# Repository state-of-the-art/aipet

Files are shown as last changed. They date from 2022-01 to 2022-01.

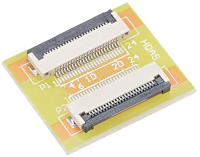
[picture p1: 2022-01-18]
doc/img/flex_to_flex.png

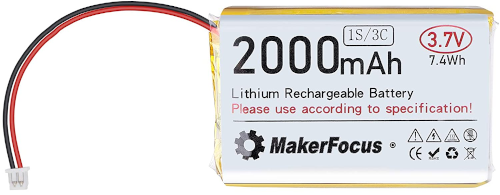
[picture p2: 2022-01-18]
doc/img/battery.png

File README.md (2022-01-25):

# AiPet

AiPet project aimed to create the AI-enchanced soft robot pet. In general it's an inflated beach
ball which contains a core with electronics and motors inside, controls pressure and position of
the core by teflon strings to move around.

It can hear by mic array, see the world via 2 cameras and use internal speakers to make noise. The
charging is wireless so it can charge itself if can find the properly placed wireless charger.

## Electric schema

Check this document to figure out: [Electric schema](doc/electric_schema.svg)

## Components

* [Sipeed Maix M1W Dock Kit K210 AI+lOT WiFi Development Board RISC-V Dual Core 64bit](https://www.amazon.com/dp/B08HJ8W1WB/)
* [Sipeed Maix Binocular Camera](https://www.amazon.com/dp/B08HH9BYTF/)
* [Sipeed Maix R6+1 Microphone Array](https://www.amazon.com/dp/B08HH799XZ/)
* [Flexible Flat Cable, 24 Pins 0.5mm Pitch 150mm FPC FFC](https://www.amazon.com/dp/B07S191XHZ/)
* [0.5mm Pitch 24 Pins to 24 Pin Extension Connector Aapter FFC FPC](https://www.amazon.com/dp/B07SWR5VP9/)
* [3.7V 2000mAh Lithium Rechargable Battery 1S 3C](https://www.amazon.com/dp/B08T6QS58J/)
* [DC 5V 9V 12V UPS Module Voltage Boost Battery Charge with Protection for Lithium Li-ion 18650 Battery](https://www.amazon.com/dp/B08LZCPVFM/)
* [6x 3V Micro Planetary Reducer Motor (9161C)](https://www.amazon.com/dp/B07N7PY71F)
* [6x custom motor driver](custom/m10_mini_dc_control/)
* [DRV8833 Motor Drive Module 1.5A Dual H Bridge](https://www.amazon.com/dp/B08RMWTDLM/)
* [2x OV2640 Camera Module T-Camera Plus Camera Module ESP32-DOWDQ6 8MB SPRAM with 1/4" OLED Fisheye Lens](https://www.amazon.com/dp/B08FC2FL79/)
* [GY-87 10DOF Module MPU6050 HMC5883L BMP180 Gyroscope Acceleration Compass](https://www.amazon.com/dp/B098JN14XV/)
* [2x Magnetic Speaker 1W 8 Ohm 20x14x3mm](https://www.amazon.com/dp/B0826YMCQ7/)
* [High Power 24V 200mm One-to-Many Long Distance Wireless Charging Pad](https://www.amazon.com/dp/B07QNF6J6Z/)

* [6x MR63ZZ 3x6x2.5mm Rolling Bearing](https://www.amazon.com/dp/B0816CL22H/)
* [16inch Clear Beach Ball](https://www.amazon.com/dp/B0943CCZLQ/)
* [6x Clear Suction Cups](https://www.amazon.com/dp/B07H5QCXR6/)
* Silicone air hose
* FDM 3D Printer

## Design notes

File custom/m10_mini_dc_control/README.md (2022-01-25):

# m10 mini dc control

This control board designed to precisely control the 9161C geared M10 mini motor with extended
shaft.

# Usage

In general you just need to connect the board to your I2C bus and power it with 5V of power (in
theory voltage regulator allows 2.5-5.5V so the motor can work on lower voltages with slower speed).

You will need to modify the `I2C_SLAVE_ADDRESS` in firmware, compile it (or use the predefined one)
and flash to the MK. After that you will be able to use as many motors as you want.

## Firmware

TODO

# Components

* 3V Micro Planetary Reducer Motor (9161C) - target motor with plastic reduction gearbox
* ATTiny 13A MMFR (DFN-10 3x3mm) - microcontroller to interface I2C and control the driver
* DRV8837C DSGR (WSON) - H-bridge driver for the motor
* MIC5365-3.3YMT-TZ (Thin MLF (MT)) - 5V to 3.3V voltage regulator to power the MK and driver logic
* QRE1113GR (100CY) - reflective object sensor to detect the motor rotation
* Various 0201 and 0402 resistors, caps and a LED

* (optional) Electrolitic capacitor to store the rest power from the motor (check driver DS)

## [3V Micro Planetary Reducer Motor (9161C)](https://www.amazon.com/dp/B07N7PY71F)

Price: $1.8 ($9 for 5pc)

### Motor specifications:

* Reduction ratio: 1:171
* Rated torque: 9.8 mN.m
* Maximum torque: 37.2 mN.m

* Rated voltage: 2.5V DC
* No-load current: 40mA
* No-load speed: 92 RPM

* Dimensions: 8x10x12mm (M10 motor)
* Planetary gearbox outer diameter: 9.9mm
* Weight: 4 grams
* Geared motor height: 19.5mm (motor + gear box)
* Output shaft: Gear with an outer diameter of 5.35mm (11 teeth)

### The following measures the motor speed under other voltages:

* Voltage: 3V
  * Current: 42mA
  * Speed: 110 RPM
* Voltage: 3.7V
  * Current: 48mA
  * Speed: 135 RPM
* Voltage: 4.2V
  * Current: 52mA
  * Speed: 154 RPM
* Voltage: 5V
  * Current: 58mA
  * Speed: 180 RPM

# How to order

Just go to your favorite PCB manufacturer and order as many boards as you want.

* [PCBWay](doc/pcbway_order.png)

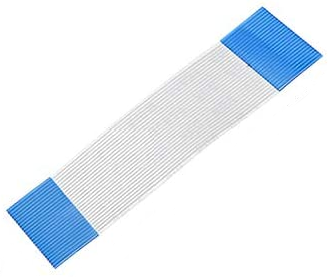
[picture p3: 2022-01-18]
doc/img/flex_camera.png

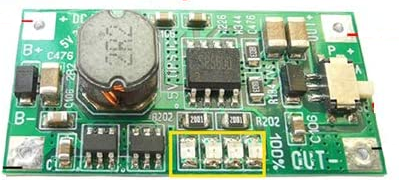
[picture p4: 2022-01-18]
doc/img/charger.png

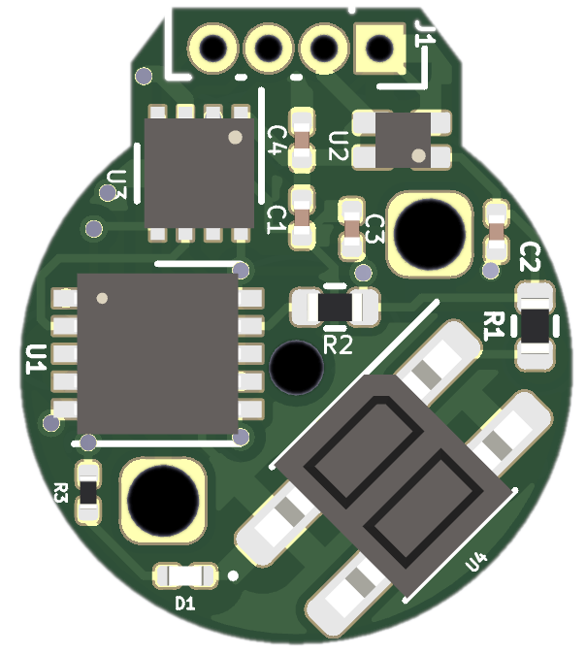
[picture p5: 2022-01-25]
doc/img/custom_motor_control.png

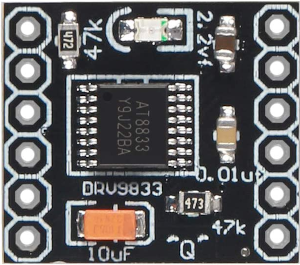
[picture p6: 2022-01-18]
doc/img/motor_driver.png

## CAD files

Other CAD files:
models/aipet.blend

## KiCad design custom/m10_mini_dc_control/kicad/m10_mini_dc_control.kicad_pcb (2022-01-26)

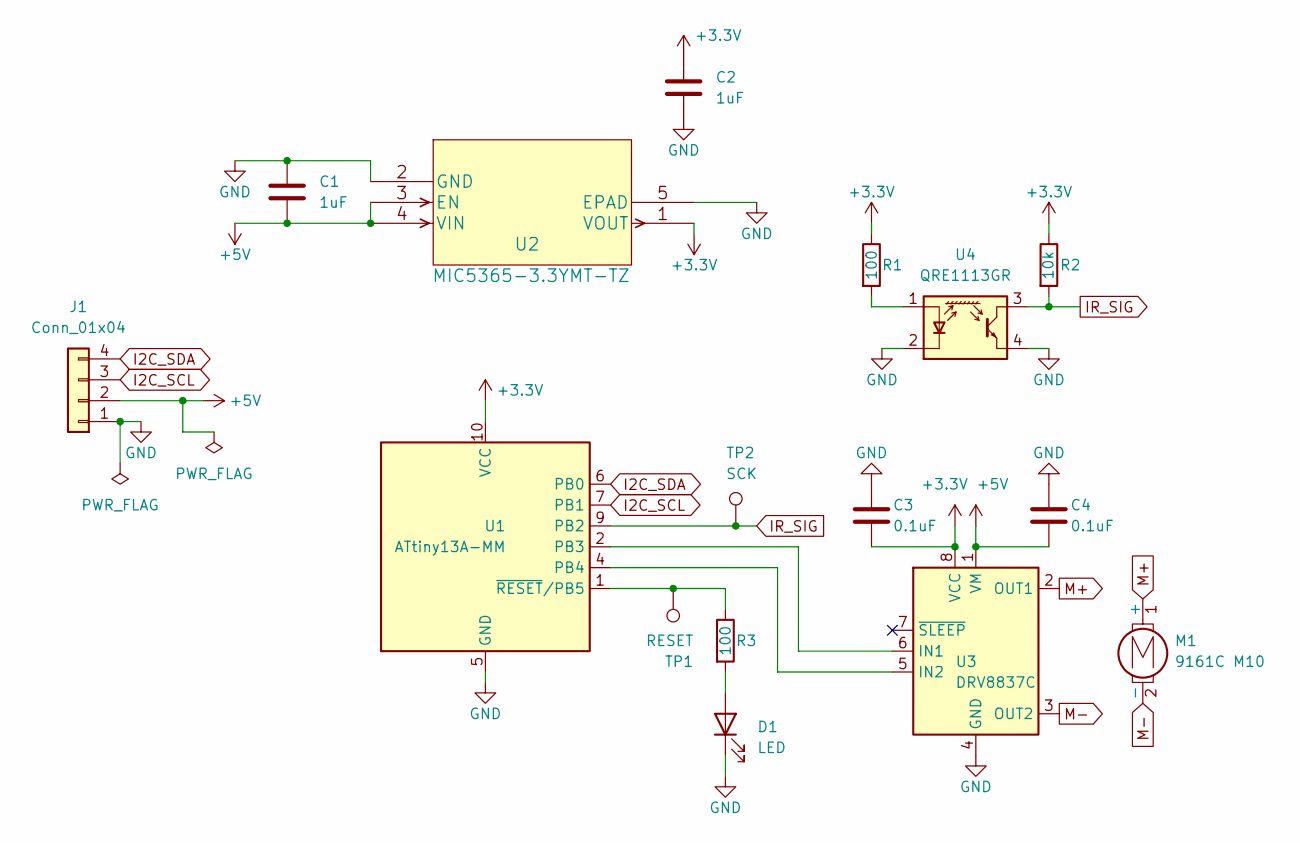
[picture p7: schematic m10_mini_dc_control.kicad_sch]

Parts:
C1, C2: 1uF; C_0201_0603Metric
C3, C4: 0.1uF; C_0201_0603Metric
D1: LED; LED_0201_0603Metric
J1: Conn_01x04; PinSocket_1x04_P1.00mm_Vertical
M1: 9161C M10; 9161C-m10-motor
R1: 100; R_0402_1005Metric
R2: 10k; R_0402_1005Metric
R3: 100; R_0201_0603Metric
TP1: RESET; TestPoint_Pad_D1.0mm
TP2: SCK; TestPoint_Pad_D1.0mm
U1: ATtiny13A-MM; DFN-10-1EP_3x3mm_P0.5mm_EP1.75x2.7mm
U2: MIC5365-3.3YMT-TZ
U3: DRV8837C; WSON-8-1EP_2x2mm_P0.5mm_EP0.9x1.6mm
U4: QRE1113GR; OnSemi_CASE100CY

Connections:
+3V3: C2.2, C3.2, R1.1, R2.1, U1.10 (VCC), U2.1 (VOUT), U3.8 (VCC)
+5V: C1.2, C4.2, J1.2, U2.3 (EN), U2.4 (VIN), U3.1 (VM)
GND: C1.1, C2.1, C3.1, C4.1, D1.1 (K), J1.1, U1.5 (GND), U1.11 (GND), U2.2 (GND), U2.5 (EPAD), U3.4 (GND), U3.9 (GND), U4.2 (K), U4.4
I2C_SCL: J1.3, U1.7 (PB1)
I2C_SDA: J1.4, U1.6 (PB0)
IR_SIG: R2.2, TP2.1, U1.9 (PB2), U4.3
M+: M1.1 (+), U3.2 (OUT1)
M-: M1.2 (-), U3.3 (OUT2)
unnamed: D1.2 (A), R3.2
unnamed: R3.1, TP1.1, U1.1 (~RESET/PB5)
unnamed: U1.4 (PB4), U3.5 (IN2)
unnamed: U1.2 (PB3), U3.6 (IN1)
unnamed: R1.2, U4.1 (A)

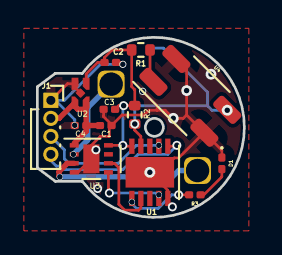
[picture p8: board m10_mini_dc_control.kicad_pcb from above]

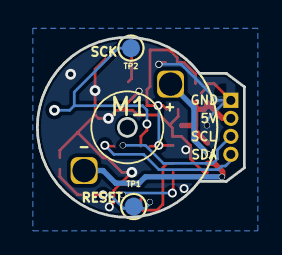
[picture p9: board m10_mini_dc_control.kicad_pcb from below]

Board: 2 copper layers, 11.5 x 10.0 mm, 16 parts (3 on the bottom side), 13 nets.

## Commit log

2022-01-18 Added the first documentation and the base model
    [aipet.blend]
2022-01-25 Added the custom control boards for the 9161C motor
    [m10_mini_dc_control.kicad_pcb, m10_mini_dc_control.kicad_sch]
2022-01-26 Fixed motor control pcb issue with not connected ground
    [m10_mini_dc_control.kicad_pcb]
2022-01-26 Made PCB 0.6mm since there is no way to reroute to drill a hole
    [m10_mini_dc_control.kicad_pcb]
